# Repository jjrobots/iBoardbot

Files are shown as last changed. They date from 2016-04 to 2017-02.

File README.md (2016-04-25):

# iBoardbot
iBoardbot project

Project page: https://www.kickstarter.com/projects/879074320/iboardbot-the-internet-controlled-whiteboard-robot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

BOM:
- GT2 timing belt (two segments of 53+100 cms)
- pulley gt2 20 tooth
- 608 bearing
- 623 bearing
- Stainless steel round bar (8mmØ,450mm length)
- 2x  round aluminium tube (6mmØ, 205 mm length)
- 4x 30 cms servo cable extender
- 2x 1.8deg NEMA 17 Stepper motors (40mm length) (4.4Kg/cm torque)
- Motor cables (14+70 cms length do the job)
- 400x150x6mm glass (for the standard iBoardbot Robot)
- 2x SG90 servo
- Arduino Leonardo
- B-robot Brain Shield 2.1
- Power supply 12v/1.5A
- 2x copper bushing (8 *11* 22) 
- 10x 6mm M3 bolts
- 5x 16mm M3 bolts
- 15x M3 nuts
- 2x M3 self locking nuts

OTHER:
- 3mm wide/100mm long zip ties (~x10)
- 5mmØ cable wrap (~60 cms)

JJROBOTS.

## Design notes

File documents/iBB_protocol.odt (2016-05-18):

iBoardbot project

Communication protocol definition

Versión: 0.4

jjrobots.

Commands and Blocks of data description

We choose a small block data size because Arduino has a very limited RAM resources (2.5k on our ATMega32U4) and we need to store the whole block in memory for processing the commands.

Block data size (packet): 768 bytes (256*3)

Comand size: 3 bytes. One block = 256 commands.

Each command has 2 fields of 12 bits: 2x12 = 24bits = 3 bytes.

C1 = 12 bits MSB, C2 = 12 bits LSB

111110100001 111110100001 = C1 C2 = total: 3 bytes (12+12 = 24 bits)

C1 C2

Command types:

- Coordinates (absolute coordinates in mm/10 units)
- Special (Pen lift, Eraser, Wait…)

Special commands:

LOGIC: C1 > 4000

C1 = 4009, C2 = 4001 : Block start. Message start sync bytes. HEX: FA9FA1

C1 = 4009, C2 < 4000 : Block number C2

C1 = 4001, C2 = 4001 : Start drawing. HEX: FA1FA1

C1 = 4002, C2 = xxxx : Stop drawing. HEX: FA2000

C1 = 4003, C2 = xxxx : Pen lift

C1 = 4004, C2 = xxxx : Pen down (draw)

C1 = 4005, C2 = xxxx : Enable Eraser

C2 = 4006, C2 = seg : Wait C2 seconds (max 30 seconds).

Coordinate commands:

LOGIC: C1 < 4000 AND C2 < 4000

C1 = X, C2 = Y. Absolute coordinates. Resolution 0.1mm

With this resolution we have a maximum 40cm x 40cm canvas size.

Standard iBoardbot canvas size is 36x12cm

DIY: For other canvas sizes, you should rescale this values on the iBoardbot firmware.

Workflow

iBoardbot poll the server with an internal iBoardbot ID and a STATUS parameters

STATUS=ready => iBoardbot is ready to receive new blocks of data (packets)

STATUS=ACK&NUM=xxx => ACK of block number xxx and ready for new blocks

Block example (draw a line):

C1 C2 [ Hexacimal]

4009 4001 [FA9FA1] # Nuevo dibujo

4009 0001 [FA9001] # Block number (this number is calculated by the server)

4001 4001 [FA1FA1] # Start drawing (new draw)

4003 0000 [FA3000] # pen lift

0000 0000 [000000] # Move to X = 0, Y = 0

1000 1000 [3E83E8] # Move to X = 100mm, Y = 100mm

4004 0000 [FA4000] # pen down (draw)

1500 1000 [5DC3E8] # Move to X = 150mm, Y = 100mm

4003 0000 [FA3000] # Pen lift

0000 0000 [000000] # Move to 0,0

4002 0000 [FA2000] # Stop drawing (Finish).

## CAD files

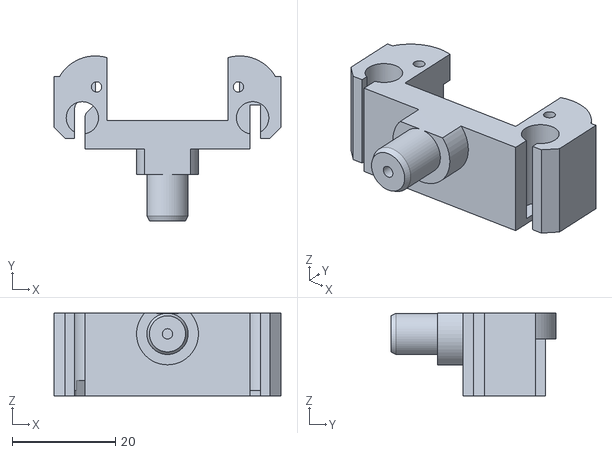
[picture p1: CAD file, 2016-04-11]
3Dparts/Bottom support Y AXIS.stl
44.0 x 32.0 x 16.0

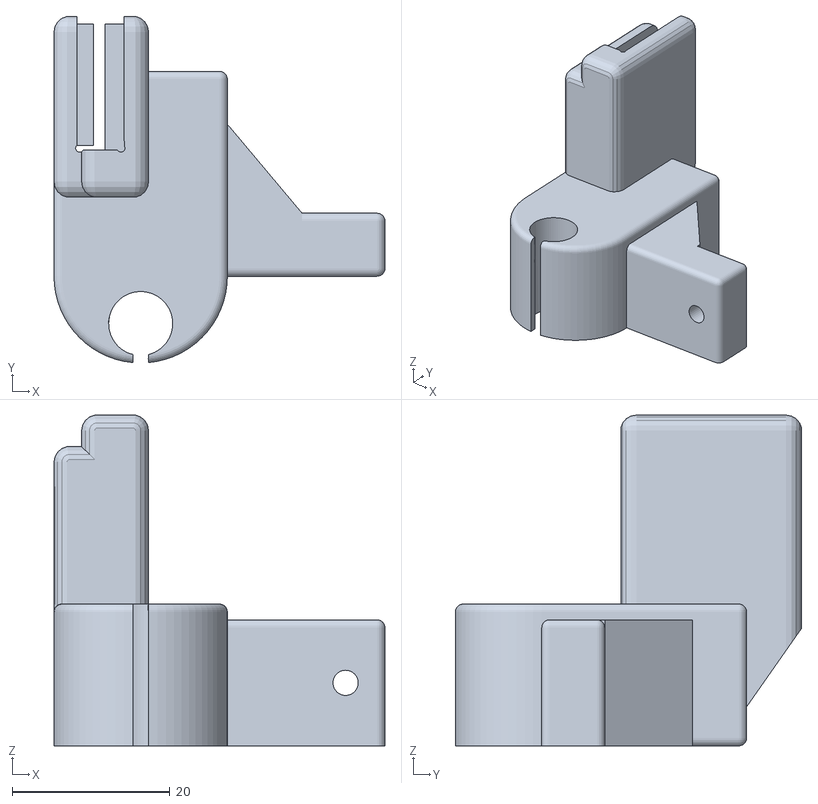
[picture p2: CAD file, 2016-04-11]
3Dparts/top RIGHT support(fixed).stl
42.0 x 43.9 x 42.0

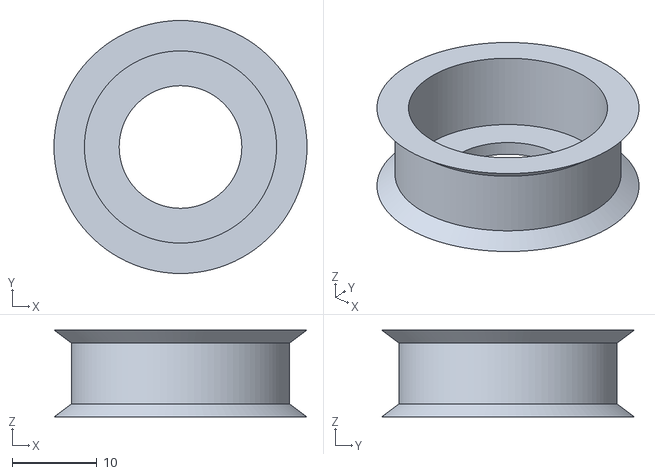
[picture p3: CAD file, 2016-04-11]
3Dparts/Pulley Y Axis.stl
29.9 x 29.9 x 10.3

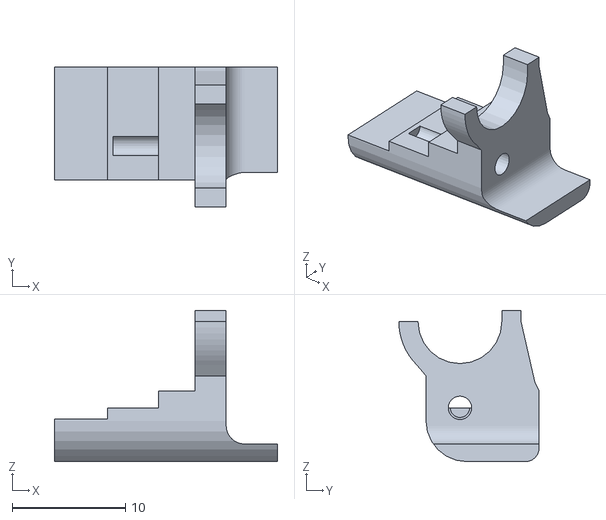
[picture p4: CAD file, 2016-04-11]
3Dparts/eraser v5 (fixed).stl
19.7 x 12.4 x 13.4

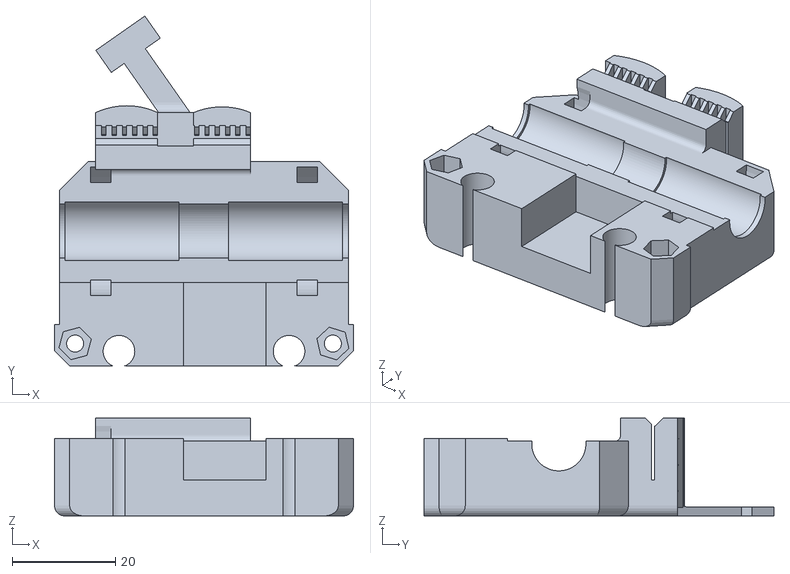
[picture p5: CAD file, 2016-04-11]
3Dparts/X AXIS carriage.stl
58.0 x 67.9 x 19.0

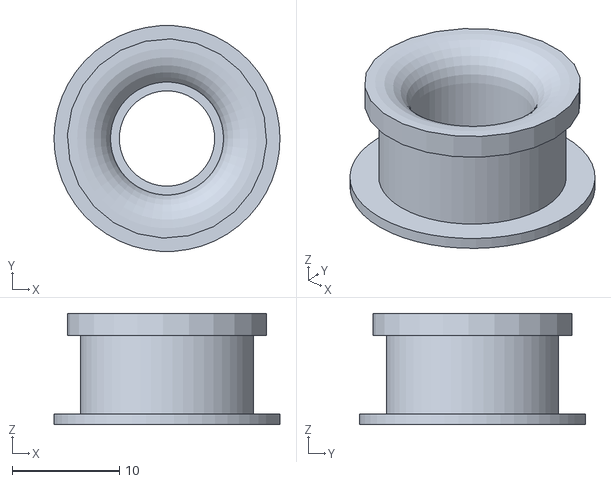
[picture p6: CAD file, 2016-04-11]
3Dparts/Pulley X axis.stl
21.1 x 21.0 x 10.4

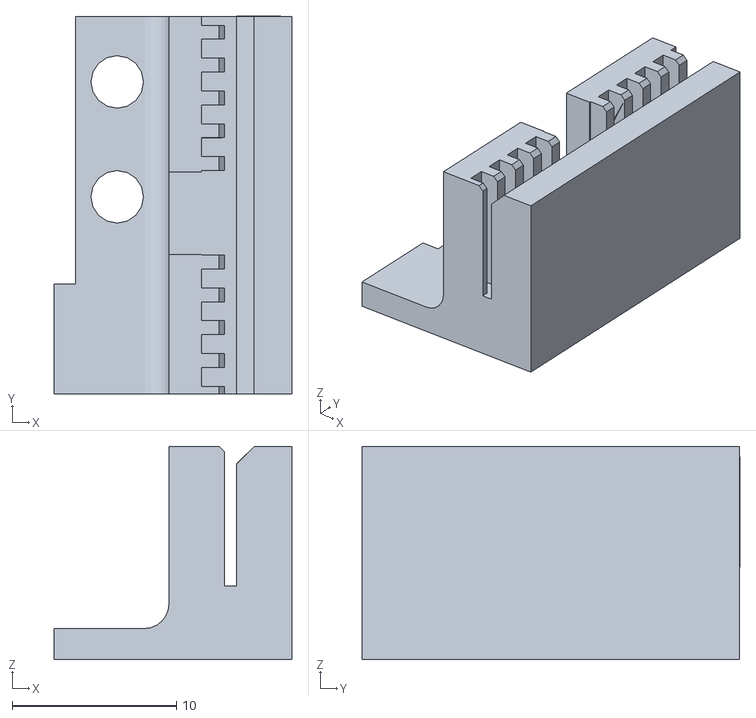
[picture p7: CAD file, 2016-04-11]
3Dparts/belt support drawing header.stl
14.5 x 23.0 x 13.0

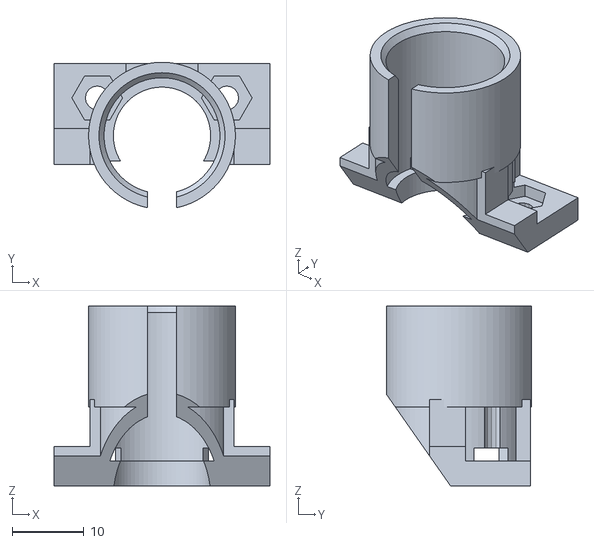
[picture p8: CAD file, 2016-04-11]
3Dparts/pen support.stl
30.0 x 20.2 x 25.0

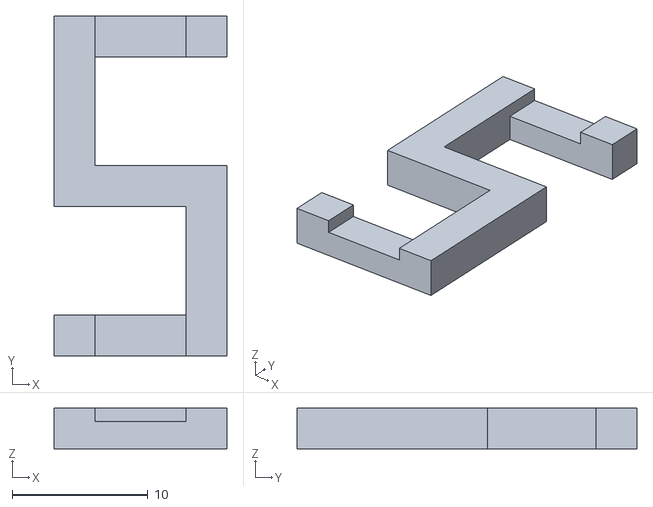
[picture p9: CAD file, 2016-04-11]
3Dparts/belt tensioner.stl
12.7 x 25.0 x 3.00

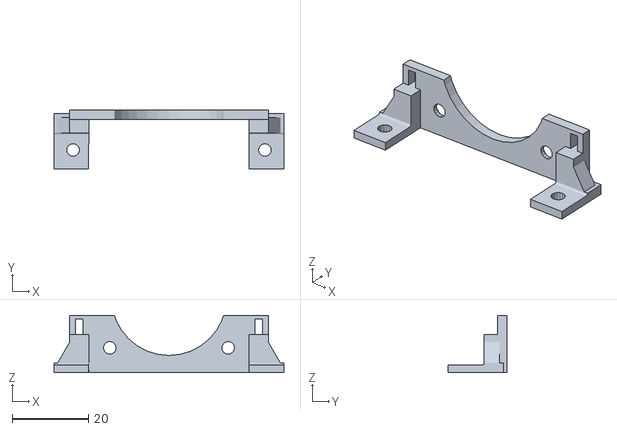
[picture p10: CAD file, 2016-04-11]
3Dparts/X motor ANGLE support.stl
60.2 x 15.5 x 15.0

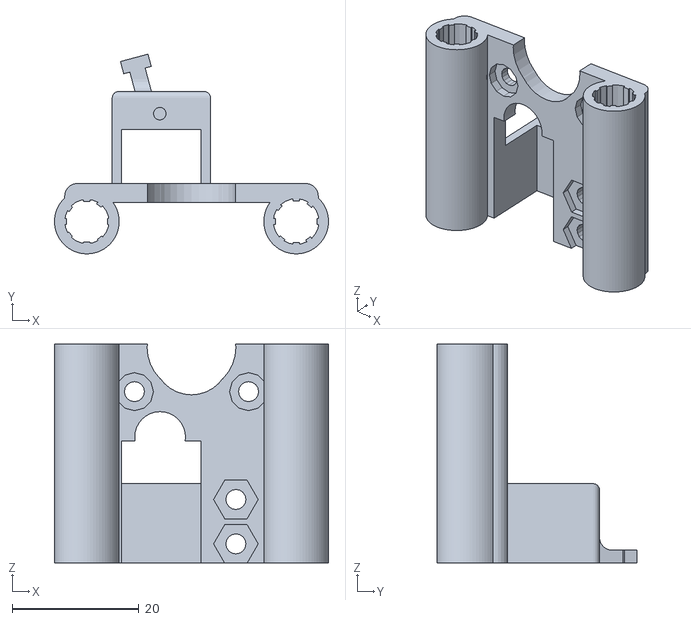
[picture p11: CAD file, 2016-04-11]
3Dparts/drawing HEADER.stl
43.2 x 31.5 x 34.5

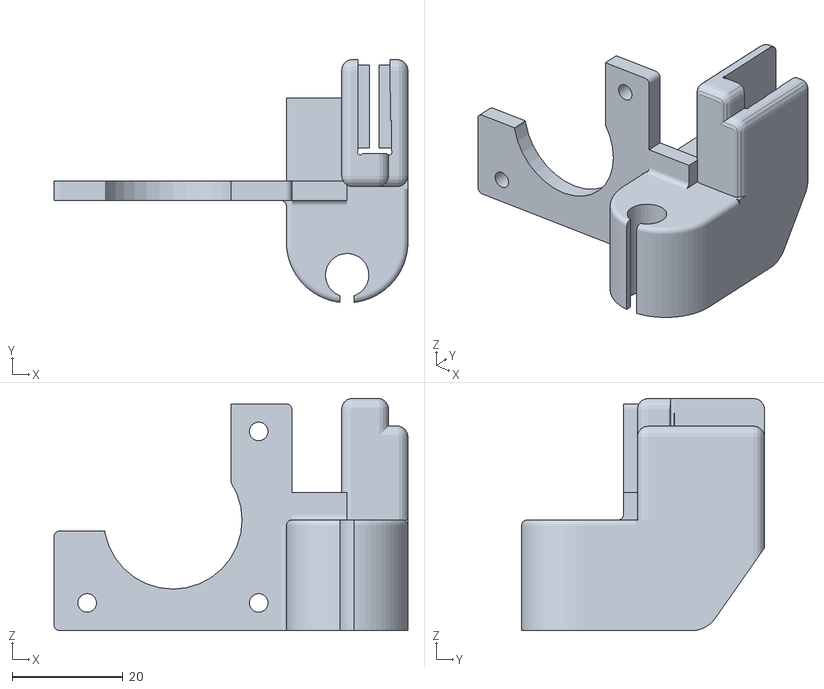
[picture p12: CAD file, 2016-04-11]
3Dparts/top LEFT support.stl
64.0 x 43.9 x 42.0

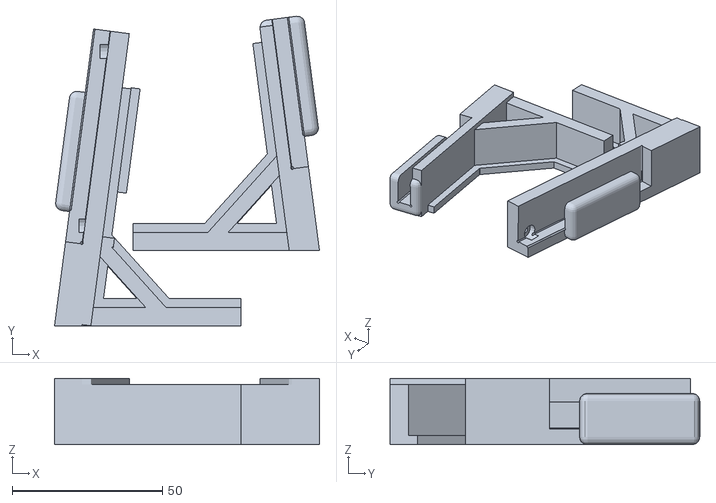
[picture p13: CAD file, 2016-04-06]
3Dparts/Legs.stl
88.2 x 103.0 x 22.0

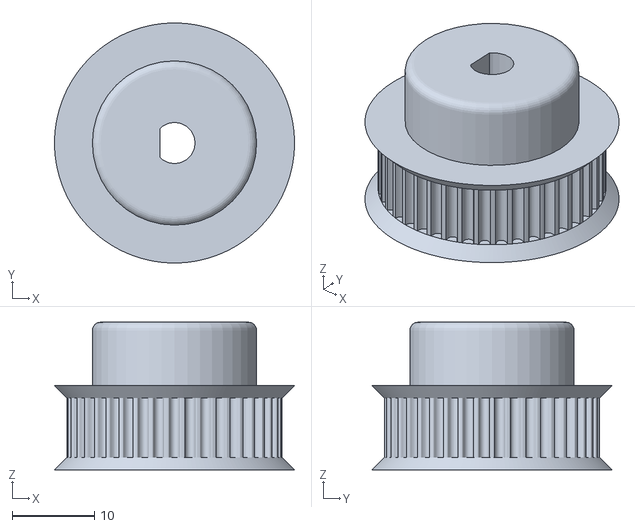
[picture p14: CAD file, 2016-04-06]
3Dparts/y_motor_pulley 42 JP.stl
29.2 x 29.2 x 18.0

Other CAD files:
3Dparts/marker SUPPORT.stl

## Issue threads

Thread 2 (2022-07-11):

http://ibbapp.jjrobots.com/ site is down since may 20th

steffenxx, 2022-07-11:
All my emails to jjrobots have been ignored so far.

:-((((((((((((((((((((((((((((((((((

MajdiQahtani, 2022-10-18:
Hi Steffen

I am experiencing the same problem.

What a shame!?

The link http://ibbapp.jjrobots.com is not accessible , and you cannot buy any of the jjRobots kits from their online store anymore.

It looks like the whole site is abandoned without any notice.

I purchased 3 of their iBoardbots which no longer work now.

Majdi

ViezeVingertjes, 2022-10-18:
I don't have one anymore, but i remember everything going through their servers.
It will make it harder to make an emulator of some sort without knowing what traffic was there to begin with.
Your best chance would be to get the code from the microcontroller and see what's happening there.

Wasn't it an Arduino? If anyone can dump the code somewhere i could always take a look.

MajdiQahtani, 2022-10-18:
Thank you Vieze for your prompt response and review of the code.

 I will take a look at the code myself and see if I can start my own iBoardbot server. I will post the results if successful.

Cheers

steffenxx, 2022-10-20:
@MajdiQahtani

This will probably be the only permanently working solution. I.e. you build a code that can be put on a local web server and then you only need to redirect the URL in the arduino code.

One more thing would be important for me. I control the iBaord via the API from my home automation. That would be important to me that the API calls, as they are documented by JJrobots, work again.

That would be wonderful and many thanks already.

I can support you with testing.

steffenxx, 2022-10-29:
@MajdiQahtani

there is already something new ? :-)
i am really looking forward to using the iBoard again.
Cheers and thanks for your support

kelsorj, 2022-12-11:
I'm experiencing the same problem and the same radio silence from JJRobot crew, really disappointing. Does anyone know if the server code is available anywhere? @MajdiQahtani?

steffenxx, 2023-01-18:
anything new in this case ?!?!?

giovan43, 2023-04-29:
hallo please would be possible a video tutorial to be able to change the web address for the board bot code and explain what to change I heard that the server name on the top page needs to be changed but how can this be done and which server or new web address should someone put there

steffenxx, 2023-10-04:
Hi, do you know the new server URL?

giovan43, 2023-10-04:
No  sorry 😣
Inviato da iPhone

> Il giorno 4 ott 2023, alle ore 23:20, steffenxx ***@***.***> ha scritto:
>
> Hi, do you know the new server URL?

Stay1444, 2024-04-19:
Ive been working on an API re-implementation since I had a board that became useless once their API went down.

It's work in progress, but it can draw SVGs and has a HTTP API to send it commands.

https://github.com/Stay1444/iboardbot

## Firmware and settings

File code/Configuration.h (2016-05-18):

// iBoardBot project
#include <stdint.h>

#define SERVER_HOST "ibb.jjrobots.com"
#define SERVER_URL "http://ibb.jjrobots.com/ibbsvr/ibb.php"
 
#define MAX_PACKET_SIZE 768

// This depends on the pulley teeth and microstepping. For 20 teeth GT2 and 1/16 => 80  200*16 = 3200/(20*2mm) = 80
#define X_AXIS_STEPS_PER_UNIT 80    
// This depends on the pulley teeth and microstepping. For 42 teeth GT2 and 1/16 => 38  200*16 = 3200/(42*2mm) = 38
#define Y_AXIS_STEPS_PER_UNIT 38 
#define X_Y_STEP_FACTOR (X_AXIS_STEPS_PER_UNIT/Y_AXIS_STEPS_PER_UNIT)

// THIS VALUES DEPENDS ON THE MOTORS, PULLEYS AND ROBOT CONSTRUCTION
#define MAX_ACCEL_X 180    //max 250      // Maximun motor acceleration in (steps/seg2)/1000
#define MAX_ACCEL_Y 110    //max 250

#define MAX_SPEED_X 30000   // Maximun speed in steps/seg (max 32000)
#define MAX_SPEED_Y 15000
#define SPEED_PAINT_X 4000   //4200 // Paint speed in steps/seg
#define SPEED_PAINT_Y 1905   //1905//2100 // Paint speed in steps/seg
#define SPEED_ERASER_X 30000 // Erase speed in steps/seg
#define SPEED_ERASER_Y 15000  // Erase speed in steps/seg

// Define speeds in steps/sec
#define MAX_SPEED_X_STEPS MAX_SPEED_X*X_AXIS_STEPS_PER_UNIT
#define MAX_SPEED_Y_STEPS MAX_SPEED_Y*Y_AXIS_STEPS_PER_UNIT

// Servo definitions
#define SERVO_NEUTRO 1450  // Servo neutral position
#define SERVO_MIN_PULSEWIDTH 900
#define SERVO_MAX_PULSEWIDTH 2100
// Servo values por NoPaint, Paint and Erase servo positions...
#define SERVO1_PAINT 1800
#define SERVO1_ERASER 1080
#define SERVO2_LIFT 1290 //1300
#define SERVO2_PAINT 1660 //1650

#define SERVO_SPEED 3   //4 // Servo move speed (higher is quicker), recommended:2

// UNCOMMENT THIS LINES TO INVERT MOTORS (by default 1)
#define INVERT_X_AXIS 1
#define INVERT_Y_AXIS 1

// Offset position in mm with respect to initial robot position (0,0)
#define ROBOT_OFFSET_X 0
#define ROBOT_OFFSET_Y 0

// Robot 
#define ROBOT_MIN_X 0
#define ROBOT_MIN_Y 0
#define ROBOT_MAX_X 358
#define ROBOT_MAX_Y 123

// Eraser offset in mm
#define ERASER_OFFSET_X 0    
#define ERASER_OFFSET_Y 0

// Offset for Paint in mm
#define PAINT_OFFSET_X 0
#define PAINT_OFFSET_Y 6

// Initial robot position in mm
// The robot must be set at this position at start time (steps initialization)
#define ROBOT_INITIAL_POSITION_X 0
#define ROBOT_INITIAL_POSITION_Y 0

#define POSITION_TOLERANCE_X 30 //24 //36
#define POSITION_TOLERANCE_Y 14 //12 //18

// Utils
#define CLR(x,y) (x&=(~(1<<y)))
#define SET(x,y) (x|=(1<<y))

#define RAD2GRAD 57.2957795
#define GRAD2RAD 0.01745329251994329576923690768489

#define MINIMUN_SPEED 25000 // Fo timer counter 

#define WIFICONFIG_MAXLEN 30

// Variable definitions
// Wifi status
bool Wconnected;
uint8_t Network_errors;

// Global variables for message reading
long message_timer_init;
uint8_t message_readed;
bool message_chunked;
int message_size;
uint8_t message_status;
int message_index;
int message_index_buffer;
char mc0,mc1,mc2,mc3,mc4,mc5,mc6,mc7;  // Last 5 chars from message for parsing...
bool show_command;
long draw_init_time;

// Log and Timer variables
long loop_counter;
long timeout_counter;
long wait_counter;
int dt;
long timer_old;
long timer_value;
int debug_counter;
int stopped_counter=0;
int delay_counter=0;
int finish=0;
uint8_t erase_mode=0;
bool poll_again = false;
bool home_position = true;
bool timeout_recover=false;

// kinematic variables
// position, speed and acceleration are in step units
volatile int16_t position_x;  // This variables are modified inside the Timer interrupts
volatile int16_t position_y;

int16_t speed_x;
int16_t speed_y;
int16_t max_speed_x;
int16_t max_speed_y;

int8_t dir_x;     //(dir=1 positive, dir=-1 negative)
int8_t dir_y;  
int16_t target_position_x;
int16_t target_position_y;
int16_t target_speed_x;
int16_t target_speed_y;
int16_t acceleration_x = MAX_ACCEL_X;
int16_t acceleration_y = MAX_ACCEL_Y;

int16_t pos_stop_x;
int16_t pos_stop_y;

uint16_t com_pos_x;
uint16_t com_pos_y;
uint16_t com_speed_x;
uint16_t com_speed_y;
int16_t last_move_x;
int16_t last_move_y;

long servo_counter;
int16_t servo_pos1;
int16_t servo_pos2;
bool servo1_ready=false;
bool servo2_ready=false;

int16_t commands_index;
int16_t commands_lines;

//EEPROM object to store Wifi configuration
struct WifiConfigS{
  uint8_t status;
  char ssid[WIFICONFIG_MAXLEN];
  char pass[WIFICONFIG_MAXLEN];
  char proxy[WIFICONFIG_MAXLEN];
  unsigned int port;
};

WifiConfigS WifiConfig;

// Some util functions...
int freeRam () {
  extern int __heap_start, *__brkval; 
  int v; 
  return (int) &v - (__brkval == 0 ? (int) &__heap_start : (int) __brkval); 
}

int16_t myAbs(int16_t param)
{
  if (param<0)
    return -param;
  else
    return param;
}

long myAbsLong(long param)
{
  if (param<0)
    return -param;
  else
    return param;
}

int sign(int val)
{
  if (val<0)
    return(-1);
  else
    return(1);
}

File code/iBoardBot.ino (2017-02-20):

// iBoardBot PROJECT
// Author: Jose Julio & Juan pedro (JJROBOTS)
// Hardware: Arduino Leonardo + JJROBOTS BROBOT shield 2 (new) with ESP-12E Wifi module
// ESP8266 firmware version 1.0.1 or higher
// Date: 18/04/2015
// Last updated: 19/02/2017
// Version: 1.08
// Project page : http://jjrobots.com/
// Kickstarter page:https://www.kickstarter.com/projects/879074320/iboardbot-the-internet-controlled-whiteboard-robot
// GIT repository: https://github.com/jjrobots/iBoardbot
// License: Open Software GPL License v2

// Hardware:
// X Motor (longitudinal move) connected to MOTOR2 output
// Y Motor (vertical move) connected to MOTOR1 output
// Eraser servo connected to Servo1 output
// PEN Lift servo connected to Servo2 output

#include <EEPROM.h>
#include <avr/pgmspace.h>

#define VERSION "iBoardBot 1.08"
//#define DEBUG 0

// ROBOT and USER configuration parameters
#include "Configuration.h"

unsigned char buffer[780];   // buffer to store incomming message from server
bool draw_task = false;
bool new_packet = false;
int block_number;
bool next_block = false;
char MAC[13];  // MAC address of Wifi module


// Configuration: Pins, servos, Steppers, Wifi...
void setup()
{
  // STEPPER PINS ON JJROBOTS BROBOT BRAIN BOARD
  pinMode(4, OUTPUT); // ENABLE MOTORS
  pinMode(7, OUTPUT); // STEP MOTOR 1 PORTE,6
  pinMode(8, OUTPUT); // DIR MOTOR 1  PORTB,4
  pinMode(12, OUTPUT); // STEP MOTOR 2 PORTD,6
  pinMode(5, OUTPUT); // DIR MOTOR 2  PORTC,6
  pinMode(A0, INPUT); // WIFI CONFIG BUTTON => sensor imput
  pinMode(13, OUTPUT); // Servo pin
  digitalWrite(A0, HIGH); // Enable Pullup on A0
  digitalWrite(4, HIGH);  // Disbale motors

  pinMode(10, OUTPUT);  // Servo1
  pinMode(6, OUTPUT);   // Servo2
  pinMode(2, OUTPUT);   // SERVOs aux (on I2C)

  delay(100);
  Serial.begin(115200); // Serial output to console
  //while (!Serial);      // Arduino Leonardo wait for Serial port to open...

  Serial1.begin(115200); // Wifi initialization

  delay(1000);

  // Manual Configuration mode? => Erase stored Wifi parameters (force A0 to ground)
  if (digitalRead(A0) == LOW)
    writeWifiConfig(0, "", "", "", 0);
  //writeWifiConfig(0,"","","",0); // Force config

#ifdef DEBUG
  delay(10000);  // Only needed for serial debug
  Serial.println(VERSION);
#endif

  // Init servos
  Serial.println(F("Servo init..."));
  servo_pos1 = SERVO1_ERASER;
  servo_pos2 = SERVO2_PAINT;
  initServo();
  moveServo1(SERVO1_ERASER);
  moveServo2(SERVO2_PAINT);
  delay(1000);
  disableServo1();
  disableServo2();

  Serial.println(F("Reading Wifi configuration..."));
  readWifiConfig();

  Serial.println(WifiConfig.status);
  Serial.println(WifiConfig.ssid);
  //Serial.println(WifiConfig.pass);
  Serial.println("****");
  Serial.println(WifiConfig.proxy);
  Serial.println(WifiConfig.port);

  // if wifi parameters are not configured we start the config web server
  if (WifiConfig.status != 1) {
    WifiConfigurationMode();
  }

  Wconnected = false;
  Network_errors = 0;
  while (!Wconnected) {
    // Wifi initialization
    Serial1.println();
    ESPflush();
    Serial1.println(F("AT+RST"));
    ESPwaitFor("ready", 10);
    Serial1.println(F("AT+GMR"));
    ESPwaitFor("OK", 5);
    GetMac();

    if (WifiConnect()) {
      digitalWrite(13, HIGH);
      Wconnected = true;
    }
    else {
      Serial.println(F("Error connecting to network!"));
      digitalWrite(13, LOW);
      delay(2500);
      Wconnected = false;
      Network_errors++;
      // If connection fail 2 times we enter WifiConfigurationMode
      if (Network_errors >= 2) {
        WifiConfigurationMode();
        Network_errors = 0;
      }
    }
  }

  // Configure TCP client (for HTTP connection to server)
  delay(250);
  Serial1.println(F("AT+CIFSR"));
  ESPwaitFor("OK", 3);
  Serial1.println(F("AT+CIPMUX=0"));
  ESPwaitFor("OK", 3);
  Serial1.println(F("AT+CIPMODE=0"));
  ESPwaitFor("OK", 3);
  Network_errors = 0;
  delay(200);

  //Initializing init position
  position_x = ROBOT_INITIAL_POSITION_X * X_AXIS_STEPS_PER_UNIT;
  position_y = ROBOT_INITIAL_POSITION_Y * Y_AXIS_STEPS_PER_UNIT;

  // Output parameters
  //Serial.print(F("Max_acceleration_x: "));
  //Serial.println(acceleration_x);
  //Serial.print(F("Max_acceleration_y: "));
  //Serial.println(acceleration_y);
  //Serial.print(F("Max speed X: "));
  //Serial.println(MAX_SPEED_X);
  //Serial.print(F("Max speed Y: "));
  //Serial.println(MAX_SPEED_Y);

  Serial.print(F("Free RAM: "));
  Serial.println(freeRam());

  // STEPPER MOTORS INITIALIZATION
  Serial.println(F("Steper motors initialization..."));
  // MOTOR1 = X axis => TIMER1
  TCCR1A = 0;                       // Timer1 CTC mode 4, OCxA,B outputs disconnected
  TCCR1B = (1 << WGM12) | (1 << CS11); // Prescaler=8, => 2Mhz
  OCR1A = MINIMUN_SPEED;               // Motor stopped
  dir_x = 0;
  TCNT1 = 0;

  // MOTOR2 = Y axis => TIMER3
  TCCR3A = 0;                       // Timer3 CTC mode 4, OCxA,B outputs disconnected
  TCCR3B = (1 << WGM32) | (1 << CS31); // Prescaler=8, => 2Mhz
  OCR3A = MINIMUN_SPEED;   // Motor stopped
  dir_y = 0;
  TCNT3 = 0;

  delay(200);
  //Serial.println("Moving to initial position...");
  // Initializing Robot command variables
  com_speed_x = MAX_SPEED_X / 2;
  com_speed_y = MAX_SPEED_Y / 2;
  max_speed_x = com_speed_x;
  max_speed_y = com_speed_y;

  //Initializing init position
  position_x = ROBOT_INITIAL_POSITION_X * X_AXIS_STEPS_PER_UNIT;
  position_y = ROBOT_INITIAL_POSITION_Y * Y_AXIS_STEPS_PER_UNIT;
  //last_position_x = position_x;
  //last_position_y = position_y;

  setSpeedS(com_speed_x, com_speed_y);
  setPosition_mm10(ROBOT_MIN_X * 10, ROBOT_MIN_Y * 10);
  last_move_x = ROBOT_INITIAL_POSITION_X * 10;
  last_move_y = ROBOT_INITIAL_POSITION_Y * 10;
  home_position = true;
  delay(50);

  // Enable TIMERs interrupts
  TIMSK1 |= (1 << OCIE1A); // Enable Timer1 interrupt
  TIMSK3 |= (1 << OCIE1A); // Enable Timer1 interrupt

  delay(50);

  ESPflush();

  Serial.println(F("Wifi parameters:"));
  Serial.print(F("Host:"));
  Serial.println(SERVER_HOST);
  Serial.print(F("Url:"));
  Serial.println(SERVER_URL);
  if ((WifiConfig.port > 0) && (WifiConfig.port < 65000) && (strlen(WifiConfig.proxy) > 0))
  {
    Serial.println(F("proxy : "));
    Serial.println(WifiConfig.proxy);
    Serial.println(F("port : "));
    Serial.println(WifiConfig.port);
  }
  Serial.println();
  Serial.println(VERSION);
  //Serial.print("ID_IWBB ");
  Serial.println(MAC);
  Serial.println(" Ready...");
  timer_old = micros();
  timeout_counter = 0;
  block_number = -1;
  commands_index = 0;
  commands_lines = 0;
  draw_task = false;

  // Ready signal
  enableServo1();
  enableServo2();
  moveServo2(SERVO2_PAINT - 200);
  delay(300);
  moveServo2(SERVO2_PAINT);
  delay(300);
  moveServo2(SERVO2_PAINT - 200);
  delay(300);
  moveServo2(SERVO2_PAINT);
  delay(1000);
  if (Wconnected) {
    moveServo2(SERVO2_PAINT - 200);
    delay(300);
    moveServo2(SERVO2_PAINT);
    delay(300);
  }

  disableServo1();
  disableServo2();
}


void loop()
{
  uint8_t response;
  char get_string[110];
  int code1;
  int code2;

  debug_counter++;
  timer_value = micros();
  dt = timer_value - timer_old;
  if (dt >= 1000) { // 1Khz loop
    timer_old = timer_value;
    loop_counter++;
    if (draw_task) {
      adjustSpeed();
      positionControl(dt);   // position, speed and acceleration control of stepper motors
      timeout_counter++;
      wait_counter = 0;
      if ((timeout_counter > 8000) || ((myAbsLong(target_position_x - position_x) < POSITION_TOLERANCE_X) && (myAbsLong(target_position_y - position_y) < POSITION_TOLERANCE_Y))) { // Move done?
        if (timeout_counter > 8000) {
          Serial.print(F("!TimeoutCounter! ")); // 8 seconds timeout
          show_command = true;
          // Reset position on timeout?
        }
#if DEBUG==2
        if (show_command) {
          Serial.print(" EP:");
          Serial.print(position_x);
          Serial.print(":");
          Serial.println(position_y);
        }
#endif
        if (commands_index < commands_lines) {
          // Reading bytes from Packet (3 bytes per command)
          int byte1 = buffer[commands_index * 3];
          int byte2 = buffer[commands_index * 3 + 1];
          int byte3 = buffer[commands_index * 3 + 2];
          // Decode the command (code1 and code2) each code is 12 bits
          code1 = (byte1 << 4) | ((byte2 & 0xF0) >> 4);
          code2 = ((byte2 & 0x0F) << 8) | (byte3);

#ifdef DEBUG
          if (show_command) {
            Serial.print(commands_index);
            Serial.print(":");
            Serial.print(code1);
            Serial.print(",");
            Serial.print(code2);
            show_command = false;
          }
#endif
          // DECODE protocol codes
          if ((new_packet) && (code1 != 4009)) { // check new packet
            // PACKET ERROR: No valid first command!
            Serial.print(F(" !PACKET ERROR!"));
            commands_index = 0;
            draw_task = false;
            disableServo1();
            disableServo2();
            servo_counter = 0;
            dir_x = 0;
            dir_y = 0;
          }
          else if (code1 == 4009) {
            new_packet = false;
            block_number = code2;
            if (block_number >= 4000)
              block_number = -1;
            else {
              Serial.print(F(" Start block:"));
              Serial.println(block_number);
            }
            show_command = true;
            servo_counter = 0;
            if (timeout_recover) {   // Timeout recovery mode? This means we had a timeout
              Serial.print(F("->Timeout recover!"));
              // Rewrite a PEN LIFT COMMAND 4003 0
              buffer[commands_index * 3] = (4003 >> 4);
              buffer[commands_index * 3+1]= ((4003 << 4) & 0xF0);
              buffer[commands_index * 3+2]= 0;
              timeout_recover = false;
              }
            else
              commands_index++;
          }
          else if ((code1 == 4001) && (code2 == 4001)) { // START DRAWING
            if (servo_counter == 0) {
              Serial.println(F(" !START DRAW"));
              enableServo1();
              enableServo2();
            }
            // Pen lift
            moveServo1(SERVO1_PAINT);
            moveServo2(SERVO2_LIFT);
            servo_counter++;
            if (servo_counter > 100) {
              digitalWrite(4, LOW); // Enable motors...
              // Default move speed
              max_speed_x = MAX_SPEED_X;
              max_speed_y = MAX_SPEED_Y;
              erase_mode = 0;
              commands_index++;
              show_command = true;
              timeout_counter = 0;
              servo_counter = 0;
            }
          }
          else if (code1 == 4002) { // END DRAWING
            Serial.print(F(" !STOP DRAW time:"));
            Serial.println(millis() - draw_init_time);
            // Pen lift
            if (!servo1_ready) {
              enableServo1();
              //Serial.println("EnableS1");
            }
            if (!servo2_ready) {
              enableServo2();
              //Serial.println("EnableS2");
            }
            moveServo1(SERVO1_ERASER);
            moveServo2(SERVO2_PAINT);
            digitalWrite(4, HIGH); // Disable motors...
            dir_x = 0;
            dir_y = 0;
            erase_mode = 0;
            draw_task = false;
            commands_index = 0;
            servo_counter = 0;
            delay(300);    // Nothing to do ??
            poll_again = true;
            if (code2 == 4010) {  // Special code? => timeout_recovery on next block
              timeout_recover = true;
              Serial.print(F("->Timeout recover mode!"));
            }
            else
              timeout_recover = false;
            //stopServo();
            disableServo1();
            disableServo2();
          }
          else if (code1 == 4003) { // Pen lift command
            if (!servo1_ready) {
              enableServo1();
            }
            if (!servo2_ready) {
              enableServo2();
            }
            moveServo1(SERVO1_PAINT);
            moveServo2(SERVO2_LIFT);
            servo_counter++;
            if (servo_counter > 90) {
              erase_mode = 0;
              commands_index++;
              show_command = true;
              max_speed_x = MAX_SPEED_X;
              max_speed_y = MAX_SPEED_Y;
              Serial.println(F(" SNP"));
              timeout_counter = 0;
              servo_counter = 0;
              disableServo2();
            }
          }
          // Pen down command
          else if (code1 == 4004) {
            if (!servo1_ready) {
              enableServo1();
            }
            if (!servo2_ready) {
              enableServo2();
            }
            moveServo1(SERVO1_PAINT);
            moveServo2(SERVO2_PAINT);
            servo_counter++;
            //Serial.println(servo_pos);
            if (servo_counter > 180) {
              servo_pos2 = SERVO2_PAINT;
              erase_mode = 0;
              commands_index++;
              show_command = true;
              max_speed_x = SPEED_PAINT_X;
              max_speed_y = SPEED_PAINT_Y;
              Serial.println(F(" SP"));
              timeout_counter = 0;
              servo_counter = 0;
              disableServo2();
            }
          }
          // Eraser command
          else if (code1 == 4005) {
            if (!servo1_ready) {
              enableServo1();
            }
            if (!servo2_ready) {
              enableServo2();
            }
            // Make position correction for eraser
            setPosition_mm10(last_move_x + ERASER_OFFSET_X * 10, last_move_y + ERASER_OFFSET_Y * 10);
            moveServo1(SERVO1_ERASER);
            moveServo2(SERVO2_PAINT);
            servo_counter++;
            //moveServo2(SERVO2_PAINT);
            //Serial.println(servo_pos);
            if (servo_counter > 350) {
              servo_pos1 = SERVO1_ERASER;
              erase_mode = 1;
              commands_index++;
              show_command = true;
              max_speed_x = SPEED_ERASER_X;
              max_speed_y = SPEED_ERASER_Y;
              Serial.println(F(" SE"));
              timeout_counter = 0;
              servo_counter = 0;
              disableServo1();
              disableServo2();
            }
          }
          // Wait command
          else if (code1 == 4006) {
            disableServo1();
            disableServo2();
            delay_counter++;
            if (code2 > 30) // maximun 30 seconds of wait
              code2 = 30;
            if (delay_counter > ((long)code2 * 1000)) { // Wait for code2 seconds
              Serial.println(F(" WM"));
              commands_index++;
              show_command = true;
              delay_counter = 0;
              timeout_counter = 0;
            }
          }
          else {
            if (servo1_ready)
              disableServo1();
            if (servo2_ready)
              disableServo2();
            timeout_counter = 0;
            // Send coordinates to robot in mm/10 units
            if (erase_mode == 1) { // In erase mode, we make the correction of the position of the eraser
              setPosition_mm10(code1 + ERASER_OFFSET_X * 10, code2 + ERASER_OFFSET_Y * 10);
              Serial.print("E");
            }
            else {
              if ((code1 < 10) && (code2 < 10)) { // Home position?
                setPosition_mm10(code1, code2);
                home_position = true;
              }
              else {
                setPosition_mm10(code1 + PAINT_OFFSET_X * 10, code2 + PAINT_OFFSET_Y * 10);
                home_position = false;
              }
            }
            last_move_x = code1;
            last_move_y = code2;
#if DEBUG>0
            Serial.print("   ");
            Serial.print(target_position_x);
            Serial.print(",");
            Serial.print(target_position_y);
#endif

#ifdef DEBUG
            Serial.println();
#endif
            commands_index++;
            show_command = true;
          }

        }
        else {
          // End of commands...
          Serial.print(F(" !FINISH! time:"));
          Serial.println(millis() - draw_init_time);
          commands_index = 0;
          draw_task = false;
          disableServo1();
          disableServo2();
          servo_counter = 0;
          dir_x = 0;
          dir_y = 0;
        }
      }

#if DEBUG==2
      if ((loop_counter % 50) == 0) {
        Serial.print(position_x);
        Serial.print(":");
        Serial.print(position_y);
        Serial.println();
      }
#endif
    }  // draw task
    else {
      // Polling server, task for me?
      loop_counter = 0;
      poll_again = false;
      if (!home_position) {
        if (wait_counter == 0)
          wait_counter = millis();
        if ((millis() - wait_counter) > 8000) {
          // Force Go to home command
          Serial.println("->Force Home!");
          draw_task = true;
          new_packet = true;
          digitalWrite(4, LOW); // Enable motors...
          show_command = true;
          timeout_counter = 0;
          // ($code1>>4),(($code1<<4)&0xF0)|(($code2>>8)&0x0F),($code2&0xFF)
          // 4009,4000
          buffer[0] = (4009 >> 4);
          buffer[1] = ((4009 << 4) & 0xF0) | ((4000 >> 8) & 0x0F);
          buffer[2] = (4000 & 0xFF);
          // 4001,4001
          buffer[3] = (4001 >> 4);
          buffer[4] = ((4001 << 4) & 0xF0) | ((4001 >> 8) & 0x0F);
          buffer[5] = (4001 & 0xFF);
          // 4003,0000
          buffer[6] = (4003 >> 4);
          buffer[7] = ((4003 << 4) & 0xF0) | ((0 >> 8) & 0x0F);
          buffer[8] = 0;
          // 1,1
          buffer[9]  = 0;
          buffer[10] = ((1 << 4) & 0xF0) | 0;
          buffer[11] = 1;
          // 4002,4002
          buffer[12] = (4002 >> 4);
          buffer[13] = ((4002 << 4) & 0xF0) | ((4010 >> 8) & 0x0F);  // Special END 4002 4010 => timeout recover
          buffer[14] = (4010 & 0xFF);
          commands_lines = 5;
          draw_init_time = millis();
          return; // End
        }
      } // if(!home_position)
      delay(20);
      Serial.println();
      Serial.println(F("POLL server..."));
      ESPflush();
      //ESPwait(1);
      if (block_number == -1) {
        // Ready for new blocks...
        strcpy(get_string, SERVER_URL);
        strcat(get_string, "?ID_IWBB=");
        strcat(get_string, MAC);
        strcat(get_string, "&STATUS=READY");
        response = ESPsendHTTP(get_string);
      }
      else {
        // ACK last block and ready for new one...
        strcpy(get_string, SERVER_URL);
        strcat(get_string, "?ID_IWBB=");
        strcat(get_string, MAC);
        strcat(get_string, "&STATUS=ACK&NUM=");
        char num[6];
        sprintf(num, "%d", block_number);
        strcat(get_string, num);
        response = ESPsendHTTP(get_string);
      }
      if (response) {
        message_readed = 0;
        message_status = 0;
        message_timer_init = millis();
        while (message_readed == 0)
          ESPwaitforMessage(30);
        if (message_readed == 2) {
          Serial.println(F("!ERROR: M Timeout"));
          Network_errors++;
          // if we have three or more consecutive Network errors we reset wifi connection
          if (Network_errors >= 3) {
            Serial.print(F("Too much network errors: Reseting..."));
            Network_errors = 0;
            digitalWrite(13, LOW);
            // Reset module
            Serial1.println();
            ESPflush();
            Serial1.println(F("AT+RST"));
            ESPwaitFor("ready", 10);
            if (WifiConnect()) {
              digitalWrite(13, HIGH);
            }
            else {
              Serial.print(F("Error trying to reconnect!"));
              digitalWrite(13, LOW);
            }
          }
        }
        else if (message_size < 6) {
          Network_errors = 0;
          Serial.print(F("Data size:"));
          Serial.println(message_size);
          if (message_size > 0) {
            Serial.print(F("Message:"));
            Serial.print((char)buffer[0]);
            Serial.println((char)buffer[1]);
          }
          block_number = -1;
          // Error message?
          if (buffer[0] == 'E') {
            Serial.println("Error Message!");
            Serial.println("Wait for next request...");
            delay(10000);
            // Something more here??
          }
          delay(100);
        }
        else {
          Network_errors = 0;
          Serial.print(F("Msize:"));
          Serial.println(message_size);
          Serial.print(F("Processing packet...lines:"));
          commands_lines = message_size / 3;
          Serial.println(commands_lines);
          commands_index = 0;
          if (message_size == MAX_PACKET_SIZE)
            Serial.println(F("MORE BLOCKS!"));
          draw_task = true;
          new_packet = true;
          digitalWrite(4, LOW); // Enable motors...
          show_command = true;
          timeout_counter = 0;
          draw_init_time = millis();
        }
      } // if (response)
    } // draw task
  } // 1Khz loop
}

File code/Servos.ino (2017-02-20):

// iBoardbot project

// Init servo on T4 timer. Output OC4B (Leonardo Pin10) servo1, OC4D (Leonardo Pin6) servo2, optional I2C output for servo2
// Servo2 compatible with OC4A (Leonardo Pin13)
// We configure the Timer4 for 11 bits PWM (enhacend precision) and 16.3ms period (OK for most servos)
// Resolution: 8us per step (this is OK for servos, around 175 steps for typical servo)

void initServo()
{
  int temp;
   
  // Initialize Timer4 as Fast PWM
  TCCR4A = (1<<PWM4A)|(1<<PWM4B);
  TCCR4B = 0;
  TCCR4C = (1<<PWM4D);
  TCCR4D = 0;
  TCCR4E = (1<<ENHC4); // Enhaced -> 11 bits

  // Reset servos to neutral position
  temp = 1500 >> 3;
  TC4H = temp >> 8;
  OCR4A = temp & 0xff;
  TC4H = temp >> 8;
  OCR4B = temp & 0xff;
 
  // Reset timer
  TC4H = 0;
  TCNT4 = 0;

  // Set TOP to 1023 (10 bit timer)
  TC4H = 3;
  OCR4C = 0xFF;

  // OC4A = PC7 (Pin13)  OC4B = PB6 (Pin10)   OC4D = PD7 (Pin6)
  // Set pins as outputs
  //DDRB |= (1 << 6);  // OC4B = PB6 (Pin10 on Leonardo board)
  //DDRC |= (1 << 7);  // OC4A = PC7 (Pin13 on Leonardo board)
  //DDRD |= (1 << 7);  // OC4D = PD7 (Pin6 on Leonardo board)

  //Enable OC4B output. OC4B is set when TCNT4=0 and clear when counter reach OCR4B
  //Enable servo2 on OC4A y OC4D
  TCCR4A |= (1 << COM4B1);
  TCCR4A |= (1 << COM4A1);
  TCCR4C |= (1 << COM4D1);
  // set prescaler to 256 and enable timer    16Mhz/256/1024 = 61Hz (16.3ms)
  TCCR4B = (1 << CS43) | (1 << CS40);
  // Enable Timer4 overflow interrupt and OCR4 interrupt
  TIMSK4 = (1 << TOIE4) | (1 << OCIE4A);
  
  servo1_ready=true;
  servo2_ready=true;
}

ISR(TIMER4_OVF_vect)
{
  SET(PORTD,1); // I2C servo2 output
}

ISR(TIMER4_COMPA_vect)
{
  CLR(PORTD,1);
}

void disableServo1()
{
  while (TCNT4<0xFF);   // Wait for sync...
  CLR(TCCR4A,COM4B1);
  servo1_ready=false;
}

void disableServo2()
{
  while (TCNT4<0xFF);   // Wait for sync...
  TIMSK4 = 0;
  CLR(TCCR4A,COM4A1);
  CLR(TCCR4C,COM4D1);
  servo2_ready=false;
}

void enableServo1()
{
  while (TCNT4<0xFF);   // Wait for sync...
  SET(TCCR4A,COM4B1);
  servo1_ready=true;
}

void enableServo2()
{
  while (TCNT4<0xFF);   // Wait for sync...
  TIMSK4 = (1 << TOIE4) | (1 << OCIE4A);
  SET(TCCR4A,COM4A1);
  SET(TCCR4C,COM4D1);
  servo2_ready=true;
}

/*
void stopServo()
{
  while (TCNT4<0xFF);   // Wait for sync...
  CLR(PORTD,1);
  TCCR4A = 0;
  TCCR4B = 0;
  TCCR4C = 0;
  TCCR4D = 0;
  TCCR4E = 0;
  TIMSK4 = 0;
  // Reset timer
  TC4H = 0;
  TCNT4 = 0;
  servo1_ready=false;
  servo2_ready=false;
}
*/

// move servo1 on OC4B (pin10)
void moveServo1(int pwm)
{
  pwm = constrain(pwm, SERVO_MIN_PULSEWIDTH, SERVO_MAX_PULSEWIDTH) >> 3; // Check max values and Resolution: 8us
  // 11 bits => 3 MSB bits on TC4H, LSB bits on OCR4B
  TC4H = pwm >> 8;
  OCR4B = pwm & 0xFF;
}

// move servo2 on OC4A (pin13)
void moveServo2(int pwm)
{
  pwm = constrain(pwm, SERVO_MIN_PULSEWIDTH, SERVO_MAX_PULSEWIDTH) >> 3; // Check max values and Resolution: 8us
  // 11 bits => 3 MSB bits on TC4H, LSB bits on OCR4A
  TC4H = pwm >> 8;
  OCR4A = pwm & 0xFF;
  OCR4D = pwm & 0xFF;  // New 2.1 boards servo2 output
}

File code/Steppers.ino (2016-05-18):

// iBoardbot project

// STEPPERS MOTOR CONTROL
// SPEED, ACCELERATION AND POSITION CONTROL using Arduino 16 bit Timer interrupts

// STEPPER MOTOR PINS (NEW)
// X MOTOR: MOTOR2 output - TIMER1
//     X-STEP: 12    (PD6)
//     X-DIR:  5    (PC6)
//     X-ENABLE: 4  (P)
// Y MOTOR: MOTOR1 output - TIMER3
//     Y-STEP: 7    (PE6)
//     Y-DIR:  8    (PB4)
//     Y-ENABLE: 4 (P)

// We control the speed of the motors with interrupts (Timer1 and Timer3) tested up to 32Khz.
// The position of the motor is controlled at 1Khz (in the main loop)

// TIMER 1 : STEPPER MOTOR SPEED CONTROL X-AXIS
ISR(TIMER1_COMPA_vect)
{
  if (dir_x == 0)
    return;

  SET(PORTD, 6); // STEP X-AXIS
  position_x += dir_x;
  __asm__ __volatile__ (
    "nop" "\n\t"
    "nop" "\n\t"
    "nop" "\n\t"
    "nop" "\n\t"
    "nop" "\n\t"
    "nop");
  CLR(PORTD, 6);
}

// TIMER 3 : STEPPER MOTOR SPEED CONTROL Y-AXIS  (2 Motors, left and right)
ISR(TIMER3_COMPA_vect)
{
  if (dir_y == 0)
    return;

  SET(PORTE, 6); // STEP Y-AXIS (Y-left)
  position_y += dir_y;
  __asm__ __volatile__ (
    "nop" "\n\t"
    "nop" "\n\t"
    "nop" "\n\t"
    "nop" "\n\t"
    "nop" "\n\t"
    "nop");
  CLR(PORTE, 6);
}

// We use a ramp for acceleration and deceleration
// To calculate the point we should start to decelerate we use this formula:
// stop_position = actual_posicion + (actual_speed*actual_speed)/(2*max_deceleration)
// Input parameters:
//    target_position_x
//    target_speed_x
//    max_acceleration_x

void positionControl(int dt)
{
  //int16_t pos_stop;
  int32_t temp;

  //SET(PORTF,3); // for external timing debug
  // dt = delta time in microseconds...
  //if ((dt<400)||(dt>1500)){
    //Serial.print("dt:");
    //Serial.println(dt);
    //}
  dt = constrain(dt, 500, 2000); // Limit dt (it should be around 1000 most times)
  
  // X AXIS
  temp = (long)speed_x * speed_x;
  temp = temp / (2000 * (long)acceleration_x);
  pos_stop_x = position_x + sign(speed_x) * temp;
  if (target_position_x > position_x){ // Positive move
    if (pos_stop_x >= target_position_x){  // Start decelerating?
      //Serial.println("Aqui");
      setMotorXSpeed(0, dt);         // The deceleration ramp is done inside the setSpeed function
      }
    else{
      //Serial.println("Aqui2");
      setMotorXSpeed(target_speed_x, dt);   // The aceleration ramp is done inside the setSpeed function
      }
  }
  else{   // Negative move
    if (pos_stop_x <= target_position_x)  // Start decelerating?
      setMotorXSpeed(0, dt);
    else
      setMotorXSpeed(-target_speed_x, dt);
  }
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

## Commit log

2016-04-06 3D parts
    3D printer parts
    [Drawing header Y axis.stl, Legs.stl, eraser v5.stl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]
2016-04-11 3D parts and BOM
    BOM and new 3D parts
    [Bottom support Y AXIS.stl, Drawing header Y axis.stl, Pulley X axis.stl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]
2016-04-11 Update BOM
2016-04-25 Update README.md
    Update pulley to 20teeth (bug)
2016-05-18 iBoardbot code
    Arduino code
    [Configuration.h]
2017-02-20 version 1.08
    Compatible with new and old boards servo2 setup
